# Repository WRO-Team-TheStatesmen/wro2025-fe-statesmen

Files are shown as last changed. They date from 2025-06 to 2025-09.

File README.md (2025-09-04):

<center><h1> The Statesmen 2025 </center>

This repository contains all of the documentation for team The Statesmen in the World Robot Olympiad 2025, Future Engineers category. This README.md file is the engineering notebook.

## Table of Contents
* [Our Team](#our-team)
  * [Atharv Baluja](#atharv-baluja)
  * [Arham Jain](#arham-jain)
  * [Yashvardhan Surana](#yashvardhan-surana)
* [Robot Photos](#robot-photos)
* [Performance Videos](#robot-videos)
* [Mobility Management](#mobility-management)
  * [Motor](#motor)
  * [Motor Driver](#motor-driver)
  * [Rear Wheel Drive](#rear-wheel-drive)
  * [Servo Motor](#servo-motor)
  * [Ackermann Steering System](#ackermann-steering-system)
  * [Robot Chassis](#chassis)
  * [Code Snippets](#code-snippets)
  * [Problems Faced and Solutions](#problems-we-faced-and-how-we-solved-them)
  * [Possible Improvements](#possible-improvements)
* [Power and Sense Management](#power-and-sense-management)
  * [Li-Ion Battery](#li-ion-battery)
  * [Buck Convertor](#lm2596-buck-converter)
  * [LiPo Battery](#lipo-battery)
  * [ESP32](#esp32-devkit-sbm)
  * [Raspberry Pi 5](#raspberry-pi-5-sbc)
  * [Camera](#camera)
  * [TF Luna LiDAR Sensor](#tf-luna-lidar-sensor)
  * [BNO055 Orientation Sensor](#bno055-orentiation-sensor)
  * [Power System Connections](#connection-diagram-for-power-system)
  * [Sensor Connections](#connection-diagram-for-sensors)
  * [Code Snippets](#code-snippets-for-components)
  * [Problems Faced and Solutions](#problems-we-faced-and-how-we-solved-them-1)
  * [Possible Improvements](#potential-improvements)
* [Obstacle Management](#obstacle-management)
  * [Open Challenge](#open-challenge)
  * [Obstacle Challenge](#obstacle-challenge)
  * [Problems Faced](#problems-we-faced-and-how-we-solved-them-2)
  * [Possible Improvements](#potential-improvements-1)
* [Engineering Factor](#engineering-factor)
* [Software Integration](#software-integration)
  * [System Architecture](#system-architecture)
  * [Communication Protocol](#communication-protocol)
  * [Code Modularity](#code-modularity)
  * [Communication API](#communication-api)
  * [Debugging](#debugging)
* [Robot Construction Guide](#robot-construction-guide)

## Our Team

### Team Photo
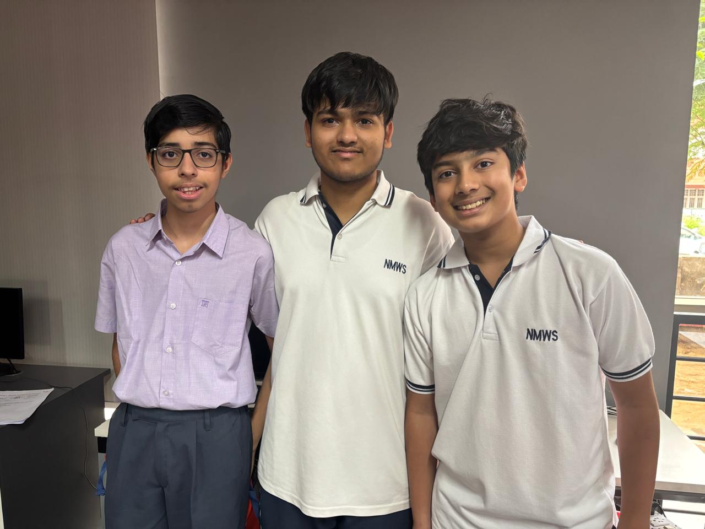
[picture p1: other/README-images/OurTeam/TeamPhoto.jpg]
Team Photo


### Atharv Baluja
<strong>Age: </strong>14

<strong> School: </strong> Neerja Modi World School

<strong>Description: </strong>
Hey! I am Atharv. I'm a high school freshman from Jaipur, India. This is my second WRO seaon. Last year, I had participated in the Future Innovator category. This year, I wanted a bigger challenge so I am participating in the Future Engineers category. I am working on the software of the robot.

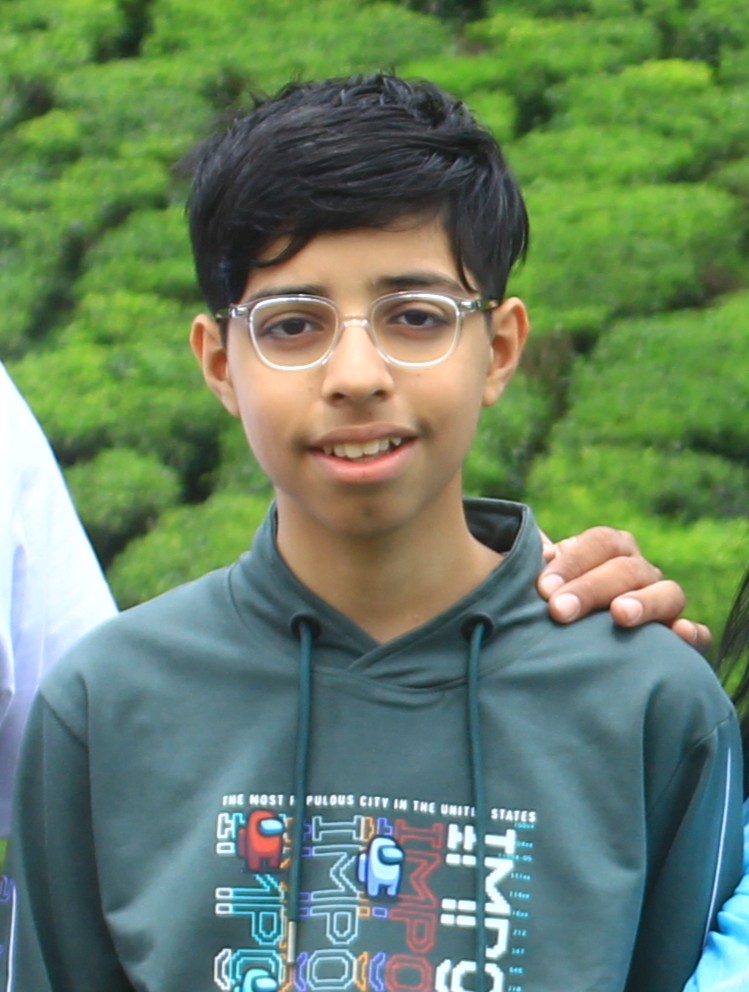
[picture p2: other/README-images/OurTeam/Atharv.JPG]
Atharv Baluja


### Arham Jain
Hello, I am Arham, an 11th-grade student at Neerja Modi School. I have competed in WRO once before in the Future Innovators category two years ago. I was preparing to compete in the Future Engineers category last year before some hurdles derailed my progress. Building on the knowledge and research from last year, I hope to put my effort into the Future Engineers Category again.

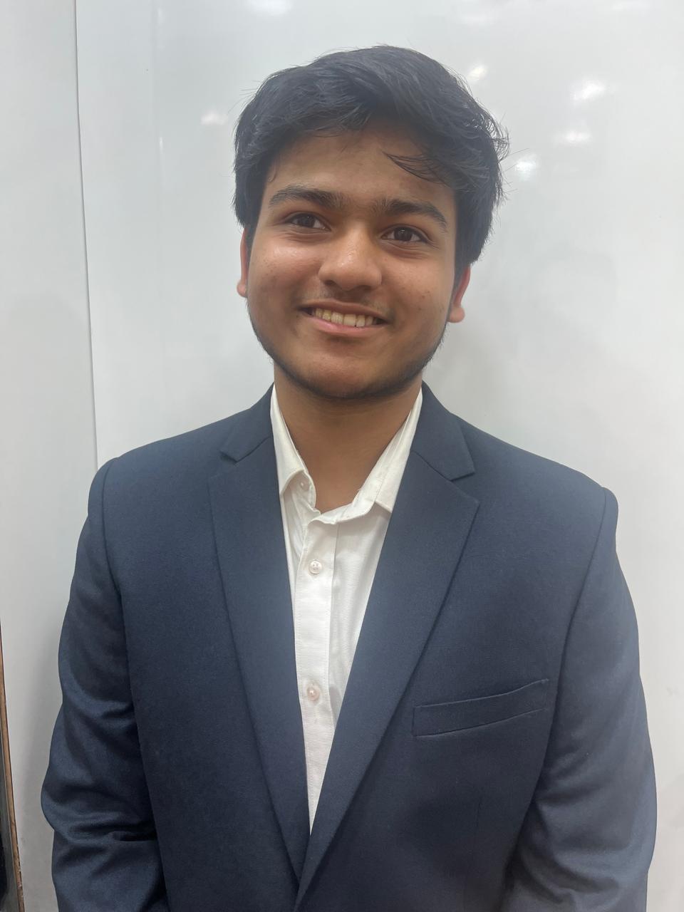
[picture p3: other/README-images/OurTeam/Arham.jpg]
Arham Jain


### Yashvardhan Surana
Hello, I'm Yash. I am a 6th grader from Jaipur. This is my second time participating in WRO. Last year, I had participated in the Future Innovators category. This year, I'm taking part in the Future Engineers category in the team The Statesmen. In The Statesmen, I am in charge of the hardware of the robot.

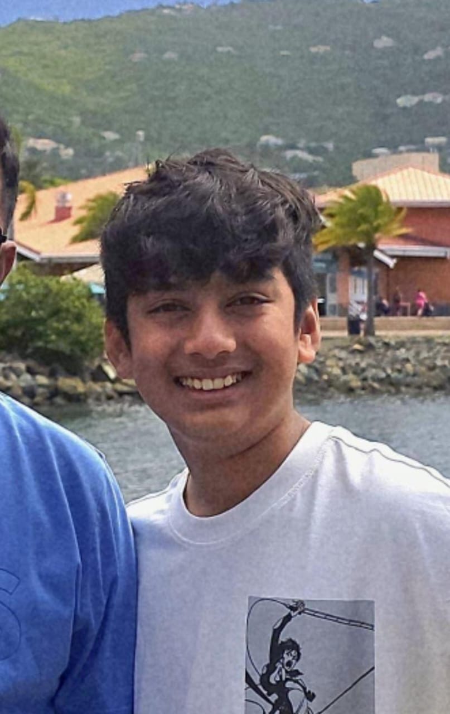
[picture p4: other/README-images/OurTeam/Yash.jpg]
Yashvardhan Surana


## Robot Photos
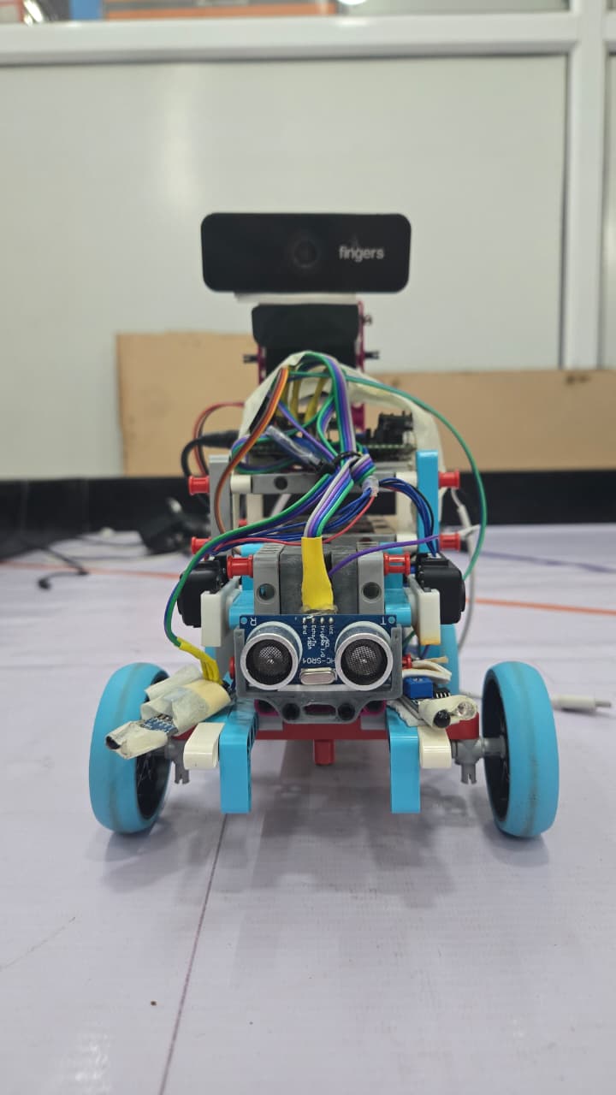
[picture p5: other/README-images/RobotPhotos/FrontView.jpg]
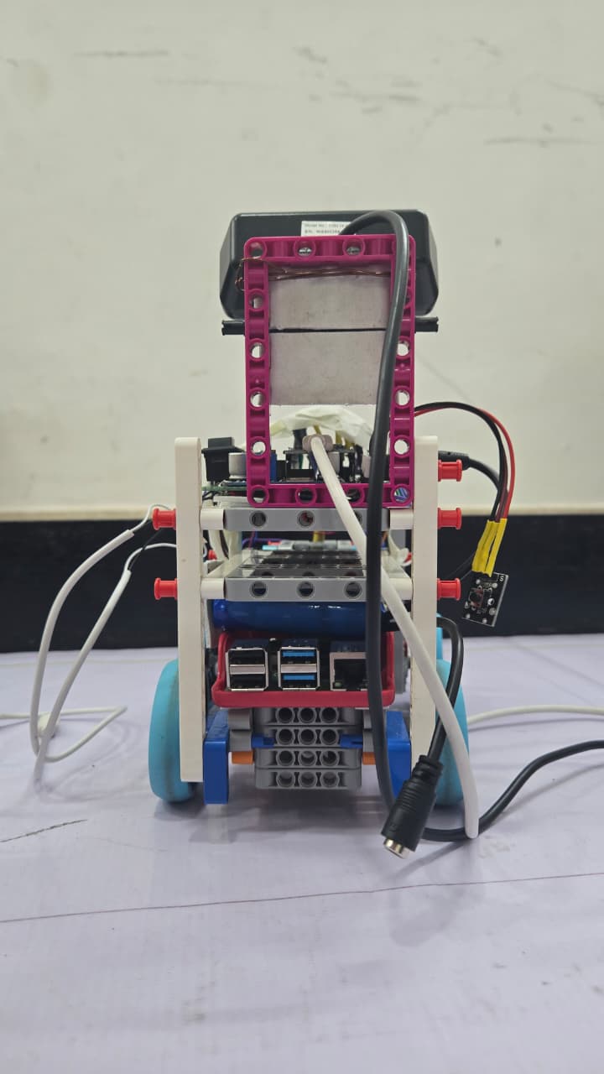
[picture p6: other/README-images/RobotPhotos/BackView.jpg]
|  |  | 
| :--: | :--: |
| *Front View* | *Back View* |
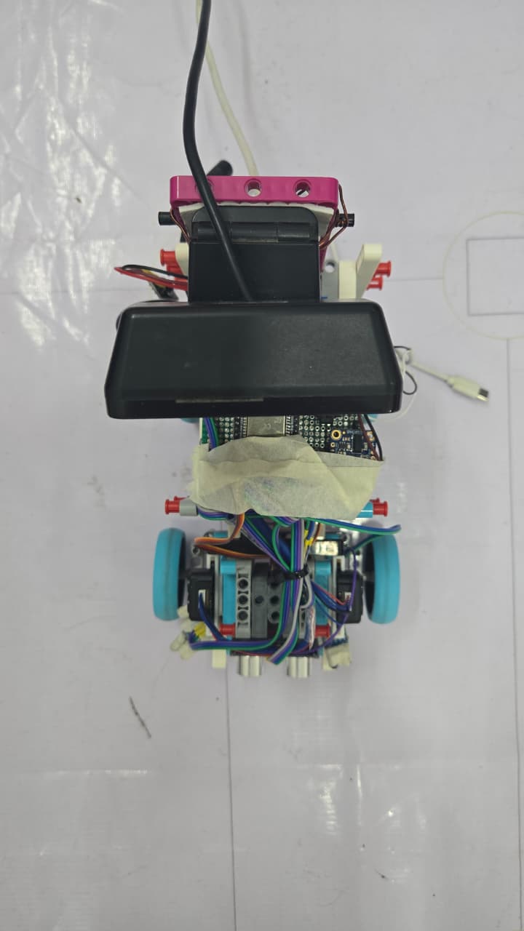
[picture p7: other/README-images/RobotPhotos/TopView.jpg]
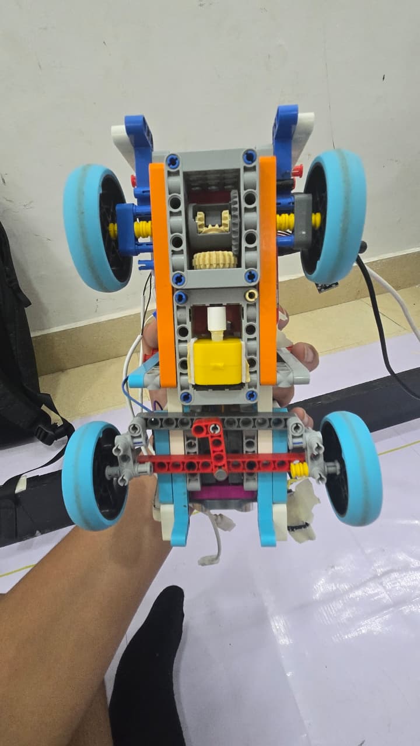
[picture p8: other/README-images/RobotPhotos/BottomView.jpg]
|  |  | 
| *Top View* | *Bottom View* |
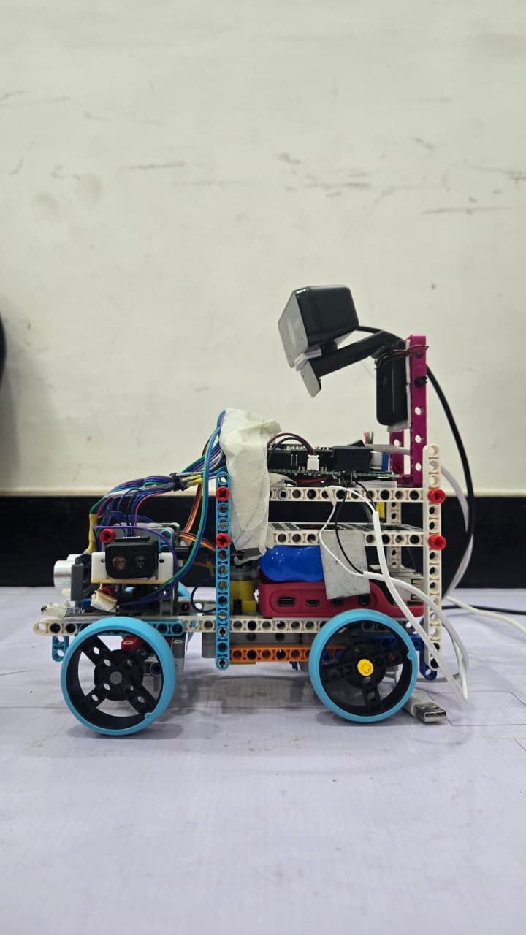
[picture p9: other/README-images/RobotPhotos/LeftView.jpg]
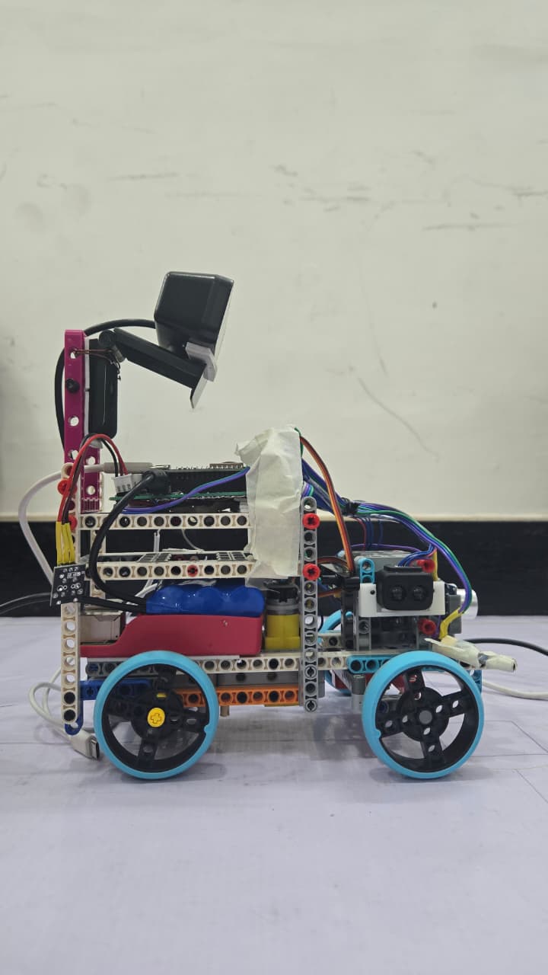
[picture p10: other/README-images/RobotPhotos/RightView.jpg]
|  |  | 
| *Left View* | *Right View* |

## Robot Videos
### Open Challenge - Default Setup
<video width="640" height="360" controls>
  <source src="./other/README-images/RunVideos/OpenChallenge1.mp4" type="video/mp4">
  Your browser does not support the video tag.
</video>

If the video is not loading for you, you can view it [here](https://youtu.be/yJYID6W3fv8)

### Open Challenge - 1 Side Extended
<video width="640" height="360" controls>
  <source src="./other/README-images/RunVideos/OpenChallenge2.mp4" type="video/mp4">
  Your browser does not support the video tag.
</video>

If the video is not loading for you, you can view it [here](https://youtu.be/VSAF0O4e32w)

### Open Challenge - 2 Sides Extended
<video width="640" height="360" controls>
  <source src="./other/README-images/RunVideos/OpenChallenge3.mp4" type="video/mp4">
  Your browser does not support the video tag.
</video>

If the video is not loading for you, you can view it [here](https://youtu.be/7XdKwXTz3Lk)

### Obstacle Challenge - Setup 1
You can view this video [here](https://www.youtube.com/watch?v=GN4vLTXXRtY)

You can watch all the videos on our [youtube channel](https://www.youtube.com/@TheStatesmen-fe)

## Mobility Management
Our robot's mobility is managed by multiple components - a BO DC motor, L293D motor driver, an MG90 servo motor connected to a Ackermann steering geometry, and a rear differential. All of these seamlessly work together to achieve efficient movement.

### Motor
Aftering considering multiple motors, we finally settleed on a DC BO motor. We considered factors like speed (RPM), torque (kg cm), weight (g), required voltage (v), and current consumption (mA).

<table>
  <tr>
    <td width="50%" style="text-align: left;">
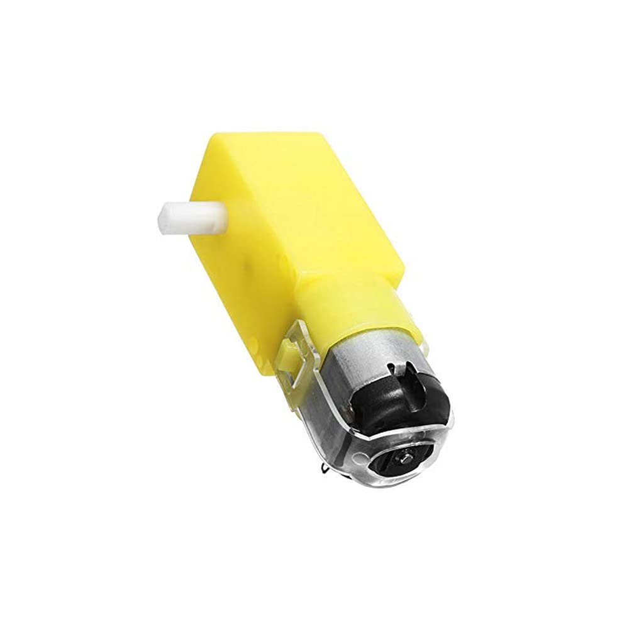
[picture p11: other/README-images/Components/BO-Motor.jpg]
DC BO Motor
      
    </td>
    <td width="50%" style="text-align: left; vertical-align: top;">
      <h3>Specifications:</h3>
      <li>Voltage: 12V</li>
      <li>Gear Ratio: 1:50</li>
      <li>Speed: 400 ± 20% rpm</li>
      <li>Rated Torque: 0.35 kg·cm</li>
      <li>Weight: 28g</li>
      <li>No Load Current Consumption: 40-180 mA</li>
      </li>
    </td>
  </tr>
</table>

You can buy this motor [here](https://robu.in/product/300-rpm-bo-motor-straight)

To connect this motor to a Lego-compatible axle, we 3D-printed a custom adapter

<table>
  <tr>
    <td width="50%" style="text-align: left;">
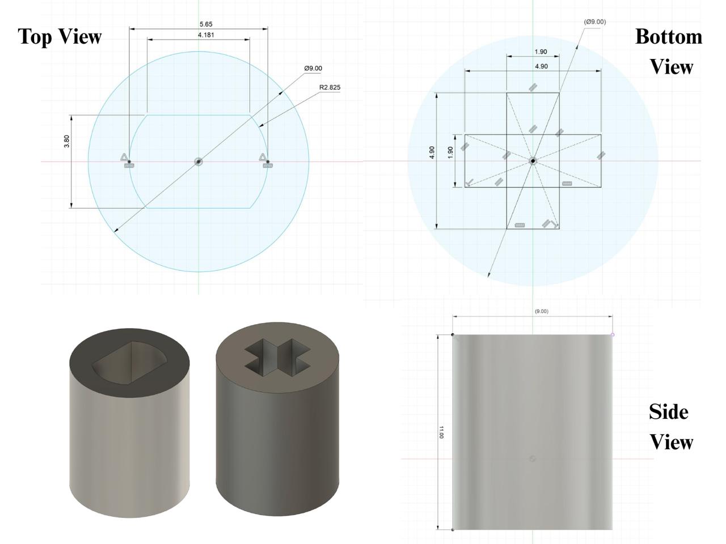
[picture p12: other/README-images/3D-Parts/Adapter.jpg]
Motor-Axle Adapter
      
    </td>
  </tr>
</table>

This is a female-to-female adapter

### Motor Driver
At first, we used the L298N Dual H-Bridge motor driver. The problem with that was that it was big because of the heatsink and the module wasn't built efficiently. After evaluating more options, we settled on the L293D motor driver. This is just like the L298N but is a small IC instead of a big module.

<table>
  <tr>
    <td width="50%" style="text-align: left;">
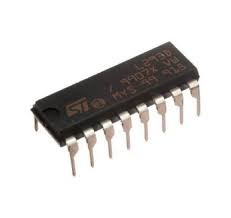
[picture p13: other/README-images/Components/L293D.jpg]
L293D Motor Driver IC
      
    </td>
    <td width="50%" style="text-align: left; vertical-align: top;">
      <h3>Specifications:</h3>
      <li>Type: Dual H-Bridge</li>
      <li>Power Supply Voltage: 4.5v to 36v</li>
      <li>Logic Voltage: 4.5v to 7v</li>
      <li>2 DC Motors</li>
      <li>Internal ESD Protection</li>
      </li>
    </td>
  </tr>
</table>

We are using the following pin connections for the motor driver:
<ol>
<li>Enable 1,2 - For PWM speed control of motor A</li>
<li>Input 1 - Direction control pin 1 for motor A</li>
<li>Output 1 - Connected to one terminal of motor A</li>
<li>GND - Ground</li>
<li>GND - Ground</li>
<li>Output 2 - Connected to other terminal of motor A</li>
<li>Input 2 - Direction control pin 2 for motor A</li>
<li>VCC 2 - Power supply (+)</li>
<li>Enable 3,4 - For PWM speed control of motor B</li>
<li>Input 3 - Direction control pin 1 for motor B</li>
<li>Output 3 - Connected to one terminal of motor B</li>
<li>GND - Ground</li>
<li>GND - Ground</li>
<li>Output 4 - Connected to other terminal of motor B</li>
<li>Input 4 - Direction control pin 2 for motor B</li>
<li>VCC 1 - Power Supply (+) for logic</li>
</ol>

### Rear Wheel Drive
We have achieved RWD with the motor connected to a lego rear differential. We have used the lego parts to minimize friction.

<table>
    <td width="50%" style="text-align: left;">
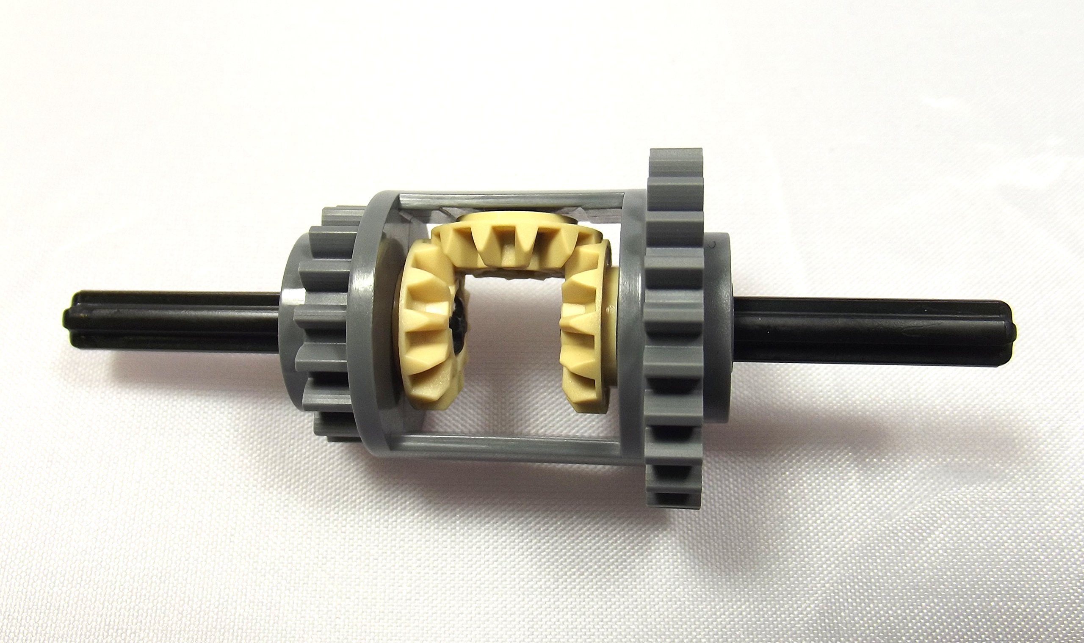
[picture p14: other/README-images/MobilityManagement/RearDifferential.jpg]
Lego Rear Differential
      
    </td>
    <td width="50%" style="text-align: left;">
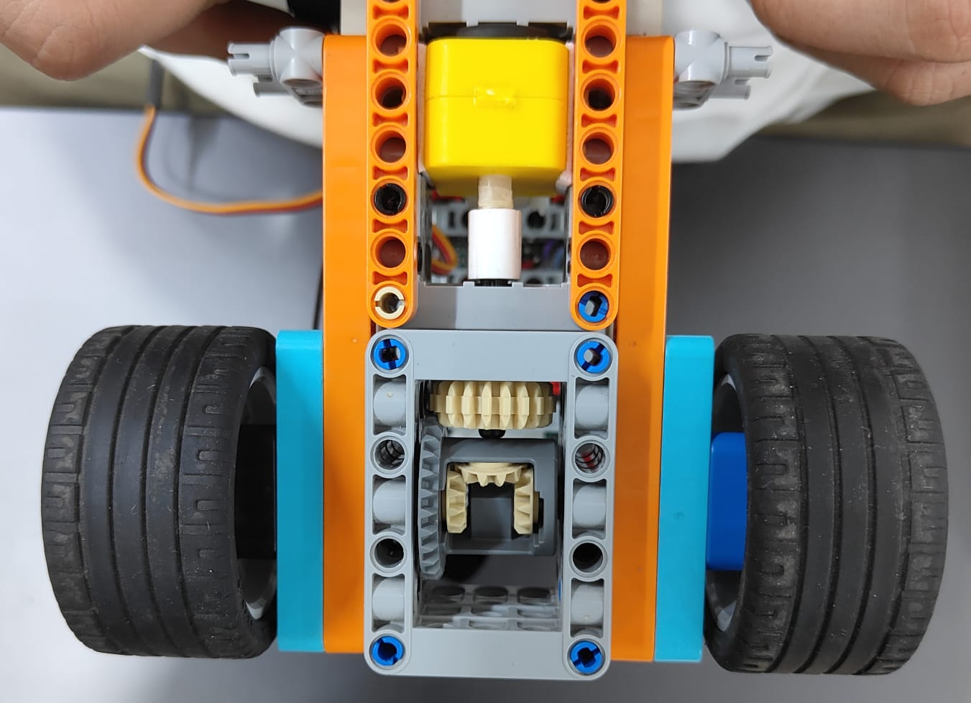
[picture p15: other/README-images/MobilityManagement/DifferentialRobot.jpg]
Lego Rear Differential
      
    </td>
</table>

Rear Differential GIF

### Servo Motor
We are using an ackermann steering geometry to steer the robot. This system runs with an MG90 servo motor.

<table>
  <tr>
    <td width="50%" style="text-align: left;">
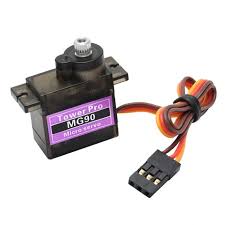
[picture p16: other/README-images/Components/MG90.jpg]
MG90 Servo Motor
      
    </td>
    <td width="50%" style="text-align: left; vertical-align: top;">
      <h3>Specifications:</h3>
      <li>Angle Constaint: 0° to 360°</li>
      <li>Input Voltage: 4.8v to 6v</li>
      <li>Stall Torque: 1.8 kg/cm</li>
    </td>
  </tr>
</table>

Here is the pinout of the MG90 Servo Motor:
<ol>
<li>VCC - Red Wire - 5V</li>
<li>Signal - Orange Wire - PWM</li>
<li>Ground - Black Wire - GND</li>
</ol>

To connect the servo motor to the steering geometry, we created a 3D-printed adapter which converted the servo rotor into a lego compatible axle.

<table>
  <tr>
    <td width="50%" style="text-align: left;">
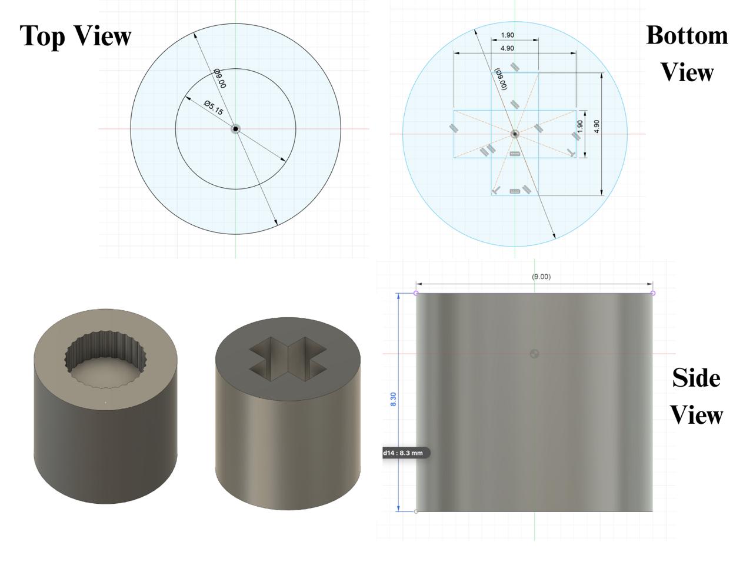
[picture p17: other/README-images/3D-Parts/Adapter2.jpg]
Servo Adapter
      
    </td>
  </tr>
</table>

It is a female-to-female adapter.

### Ackermann Steering System

We are using the Ackermann steering system. This system allows the front 2 wheels to turn at different angles, allowing for sharper turns and decreasing friction due to drag.

<table>
  <tr>
    <td width="50%" style="text-align: left;">
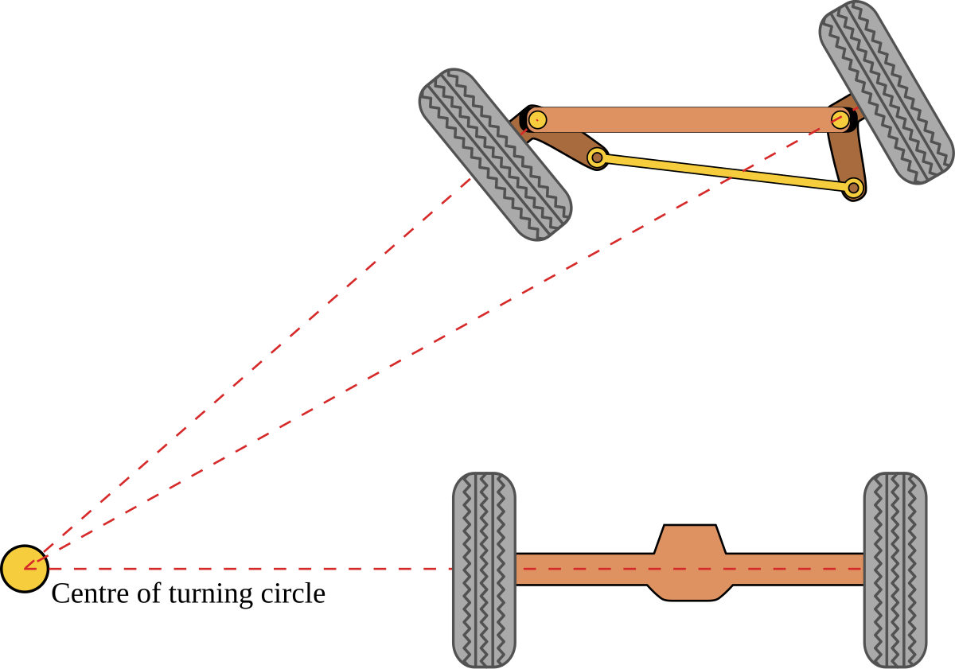
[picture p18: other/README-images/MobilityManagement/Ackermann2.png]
Ackermann Steering
      
    </td>
  </tr>
  <tr>
    <td width="50%" style="text-align: left;">
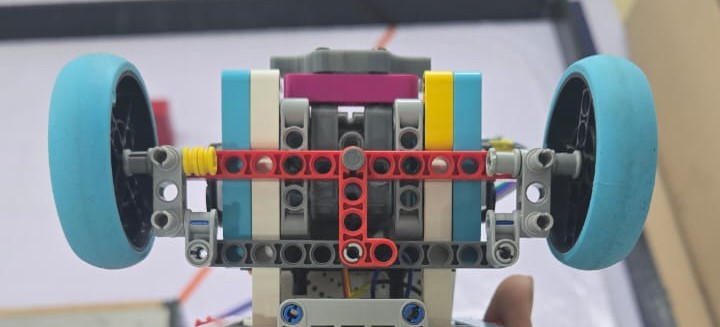
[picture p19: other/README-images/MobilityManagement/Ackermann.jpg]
Ackermann Steering
      
    </td>
  </tr>
</table>

Steering System GIF

### Chassis
#### Photos
|  |  | 
| :--: | :--: |
| *Orthographic View 1* | *Orthographic View 2* |
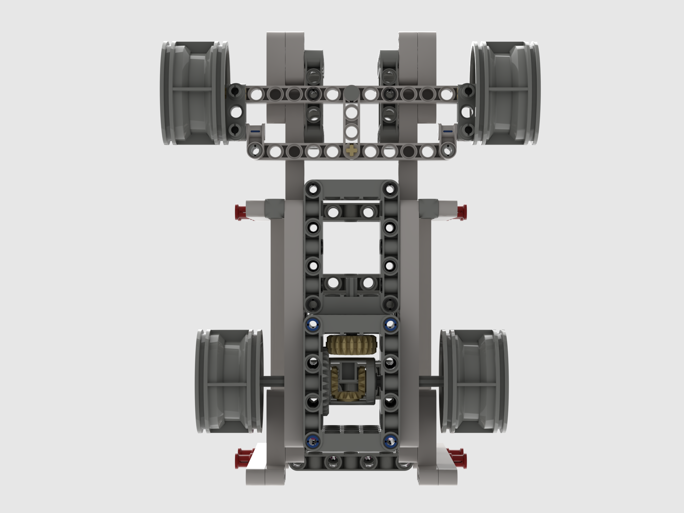
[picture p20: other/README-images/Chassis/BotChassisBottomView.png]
|  |  | 
| *Top View* | *Bottom View* |
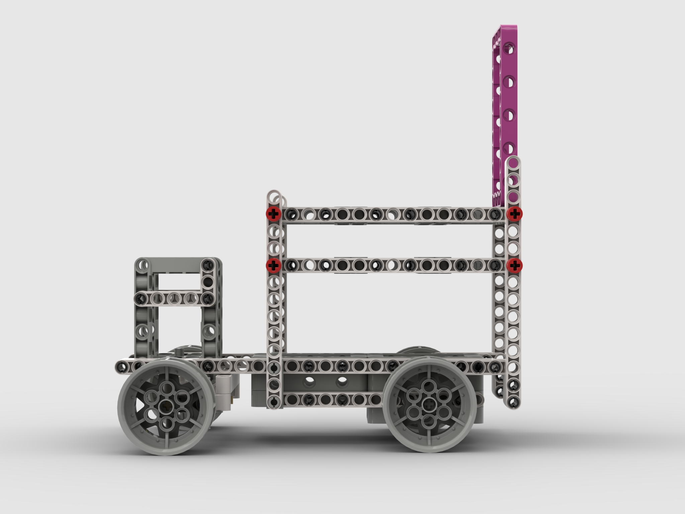
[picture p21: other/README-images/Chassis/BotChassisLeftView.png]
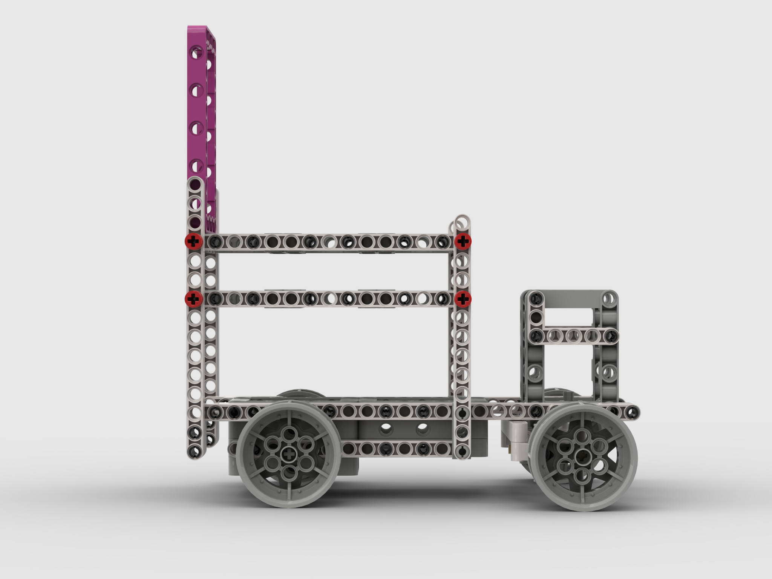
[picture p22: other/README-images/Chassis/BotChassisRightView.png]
|  |  | 
| *Left View* | *Right View* |

Robot Chassis GIF

#### Assembly Guide

<embed src="./other/README-images/Chassis/ChassisAssembly.pdf" type="application/pdf" width="100%" alt="Chassis Assembly Guide PDF"> </embed>

If the PDF is not loading properly, you can view the guide [here](https://github.com/WRO-Team-TheStatesmen/wro2025-fe-statesmen/blob/main/other/README-images/Chassis/ChassisAssembly.pdf)

### Connection Diagram for Mobility System
<table>
  <tr>
    <td width="50%" style="text-align: left;">
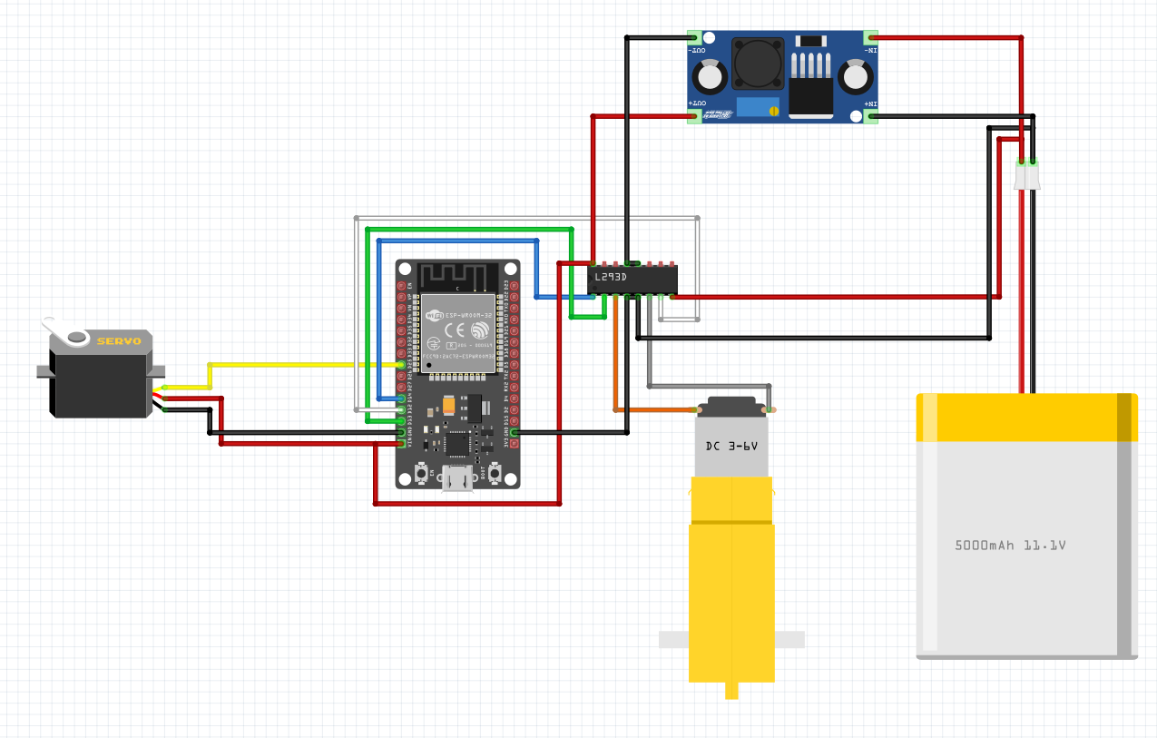
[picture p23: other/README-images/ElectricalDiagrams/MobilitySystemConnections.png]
Mobility System Connections
      
    </td>
  </tr>
</table>

### Code Snippets
#### Running the L293D Motor Driver with an ESP32 Devkit
```
// Program for running the motors via the L293D motor driver IC on an ESP32 devkit

#define IN1 13
#define IN2 12
#define ENA 14

void setup() {
  pinMode(IN1, OUTPUT);
  pinMode(IN2, OUTPUT);
  pinMode(ENA, OUTPUT);
}

void loop() {
  // Forward
  digitalWrite(IN1, HIGH);
  digitalWrite(IN2, LOW);
  analogWrite(ENA, 255);
  delay(2000);

  // Stop
  analogWrite(ENA, 0);
  delay(1000);

  // Backwards
  digitalWrite(IN1, LOW);
  digitalWrite(IN2, HIGH);
  analogWrite(ENA, 255);
  delay(2000);

  // Stop
  analogWrite(ENA, 0);
}
```

#### Running the MG90 Servo Motor with an ESP32 Devkit
```
// Program for rotating the steering MG90 servo motor connected to an ESP32 devkit [signal pin = 25]

const int servoPin = 25;
const int servoCenter = 138; // Servo center is the position of the servo at which the steering system is centered

void moveServoAngle(int angle){
  angle = constrain(angle,0,180);
  int pulsewidth = map(angle,0,180,500,2400);
  digitalWrite(servoPin, HIGH);
  delayMicroseconds(pulsewidth);
  digitalWrite(servoPin, LOW);
  delay(20 - pulsewidth/1000);
}

void steer(int angle) {
  moveServoAngle(servoCenter + angle);
}

void setup() {
  pinMode(servoPin, OUTPUT);
}

void loop() {
  steer(0);
  delay(1000);
  steer(30);
  delay(1000);
  steer(0);
  delay(1000);
  steer(-30);
  delay(1000);
}
```

### Problems We Faced and How We Solved Them
<ol>
<li> <strong>Bot Rear Skidding: </strong> At first, we were not using a rear differential but rather the motor connected to a gear which rotated a single axle which both the wheels were on. There was a huge problem with this. As shown in the image below, both wheeels have to move a different distance.<br><br>

<table>
  <tr>
    <td width="50%" style="text-align: left;">
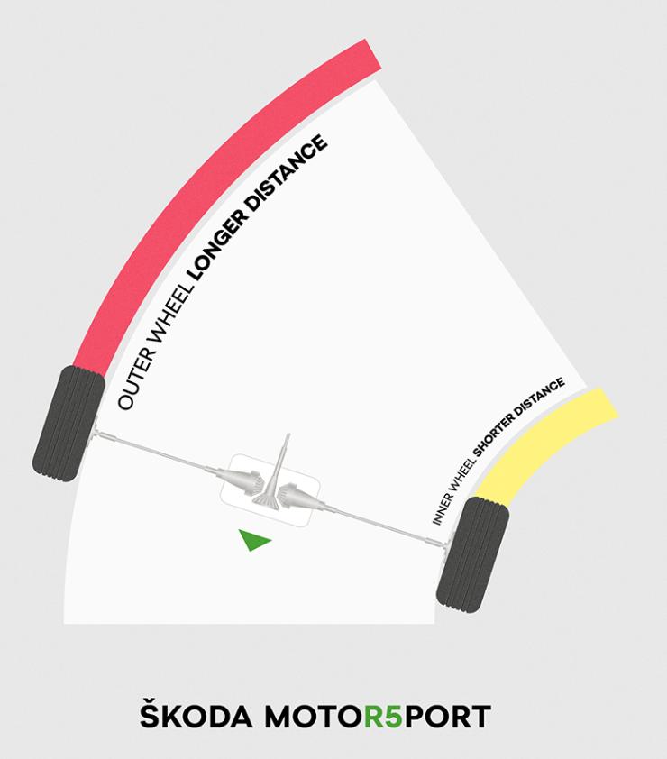
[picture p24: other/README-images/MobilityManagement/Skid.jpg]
Wheel Distance Difference
      
    </td>
  </tr>
</table>

To fix this, we added the <strong>Rear Differential</strong>. This allows the 2 wheels to move at different speeds while only using one motor.
</li>
<li> <strong>Bot Front Skidding: </strong> At first, we were using a parallel steering geometry. The same problem occurred. There was a lot of friction and drag. This limited the maximum turning angle of the robot.
<br><br>

Steering System GIF

As you can see, in this system, both the wheels are turned equally. This does not achieve peak efficiency. That is why we switched to the ackermann system.
</li>

<li>
<strong>Axle Sliiping Out of Differential</strong>

Initially, the axle used in the differential was too small. Because of vibrations, it often slipped out of the differential, which caused the gears to come out and completely ruined the robot's movement. If we used longer axles, it would stick out of the robot and could touch other blocks.

To fix this, we did two things. Firstly, we structured the chassis of the robot since there were some redundant pieces. We also switched out the rear tyres to the normal blue tyres since it would fix the problem without causing a significant change in the movement of the robot.
</li>

<li>
<strong>No Exact Piece for Ackermann</strong>: While trying to create the ackermann steering geometry, we noticed that no single piece could create the steering geometry. At first, we used this piece:

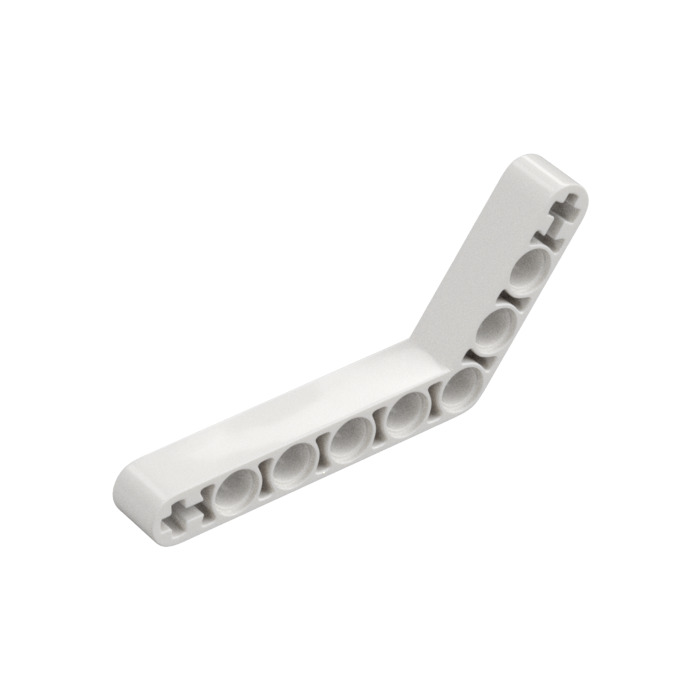
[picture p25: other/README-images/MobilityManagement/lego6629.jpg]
Lego Piece 6629


However, using this caused a problem that the robot wasn't fully level. After trying out multiple options, we finally settled on joining 2 pieces to achieve this:

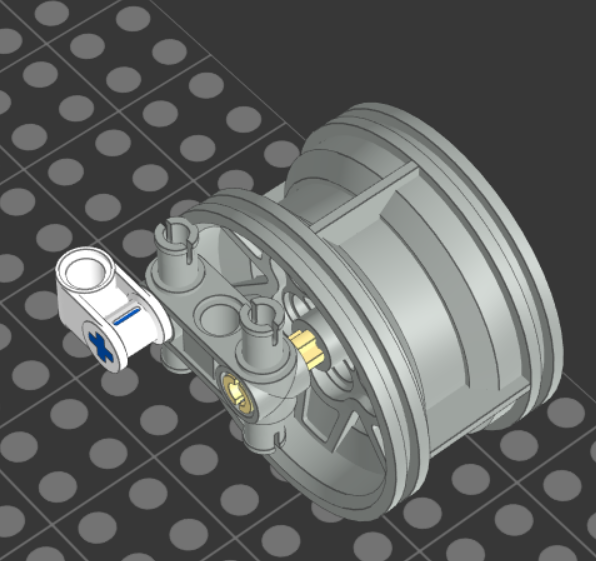
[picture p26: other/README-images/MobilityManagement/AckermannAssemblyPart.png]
Ackermann Assembly Part


With this, we encountered another problem. If we tried to turn it more than 40 degree, it would cause a lot of tension and the 2 pieces would disconnect. To increase the maximum turning angle to 60 degrees, we had to superglue the 2 pieces together.
</li>
</ol>

### Possible Improvements
<ol>
<li><strong>Using a Higher RPM Motor</strong> so that the robot can move faster</li>
<li><strong>Using a Motor with an Encoder</strong> so that the robot movements become more accurate and precise</li>
<li><strong>Using Metal Gears for the Rear Differential</strong> so that it can withstand higher speeds</li>
<li><strong>Using a Heat Sink or Active Cooling for the Motor Driver</strong> so that it doesn't get too hot much while being used</li>
<li><strong>Using Four-Wheel Drive</strong> for better movement</li>
<li><strong>Using All-Wheel Steering</strong> for better and faster turning</li>
<li><strong>Using a Custom Gearbox</strong> instead of relying on the BO motor's gear ratio to create an optimized gear ratio</li>
<li><strong>Using a Fully 3D Printed Chassis</strong> instead of using lego parts so that the robot is as light as possible</li>
</ol>

## Power and Sense Management
Our robot uses an 11.1v Li-ion Battery and a 2500 mAh 3C 11.1v LiPo battery for power with a buck converter. An ESP32 Devkit single board microcontroller is used with a Raspberry Pi 5 single board computer. Along with this, 4 TF Luna LiDAR sensors (one at the left, two at the front, and one at the back) are used for disance measurement and a BNO055 orientation sensor to measure the rotation.

### Li-Ion Battery
We are using an 11.1v Li-ion battery pack
<table>
  <tr>
    <td width="50%" style="text-align: left;">
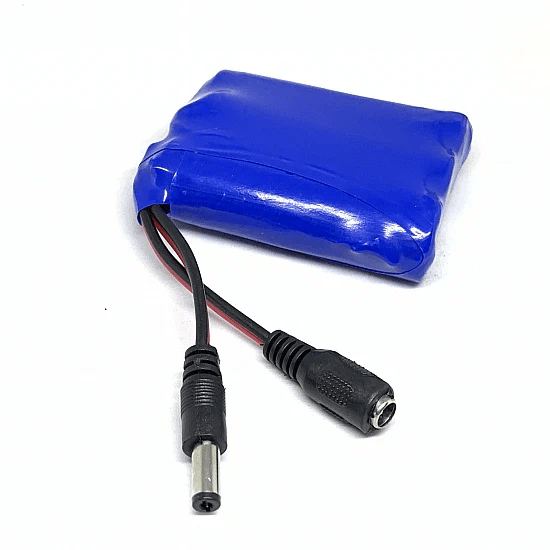
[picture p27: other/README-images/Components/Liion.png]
11.1V Li-ion Battery
      
    </td>
    <td width="50%" style="text-align: left; vertical-align: top;">
      <h3>Specifications:</h3>
      <li>Voltage: 11.1V</li>
      <li>Capacity: 2200mAh</li>
      <li>Discharge Rate: 2C</li>
      <li>Maximum Current: Capcity x Discharge Rate = 4.8A</li>
    </td>
  </tr>
</table>

This battery pack consists of 3 18650 3.7v Li-ion cells

This battery powers the motors, ESP32, and all the sensors

You can buy this battery [here](https://www.amazon.in/2200MAH-Rechargeable-Battery-Robotics-Vehicle/dp/B0DNZJ7823/)

### LM2596 Buck Converter
We are using an 11.1v battery, but the ESP32 requires 5v to be provided to it. To convert the 11.1v to 5v, we are using an LM2596 DC-DC Buck Converter

<table>
  <tr>
    <td width="250x" style="text-align: left;">
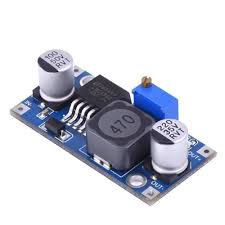
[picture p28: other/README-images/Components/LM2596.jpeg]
LM2596 Buck Converter
      
    </td>
    <td width="500px" style="text-align: left; vertical-align: top;">
      <h3>Specifications:</h3>
      <li>Supply Voltage: 3v - 40v</li>
      <li>Output Voltage: 1.5v - 35v (adjustable) --> Set to 5v for us</li>
      <li>Output Current: Rated 2A, Maximum 3A</li>
      <li>Switching Frequency: 150KHz</li>
      <li>Conversion Efficiency: 92%</li>
    </td>
  </tr>
</table>

You can buy the LM2596 Buck Converter [here](https://robu.in/product/lm2596s-dc-dc-buck-converter-power-supply/)

### LiPo Battery
We are using a lithium polymer (LiPo) battery to power the Raspberry Pi.
<table>
  <tr>
    <td width="250x" style="text-align: left;">
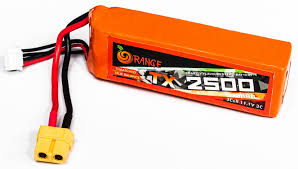
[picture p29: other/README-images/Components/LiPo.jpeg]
LiPo battery
      
    </td>
    <td width="500px" style="text-align: left; vertical-align: top;">
      <h3>Specifications:</h3>
      <li>Output Voltage: 11.1v</li>
      <li>Capacity: 2500 mAh</li>
      <li>Discharge Rate: 3C</li>
      <li>Maximum Current: 3C * 2.5Ah = 7.5A</li>
    </td>
  </tr>
</table>

### ESP32 Devkit SBM
We are using an ESP32 Devkit single board microcontroller.

<table>
  <tr>
    <td width="250x" style="text-align: left;">
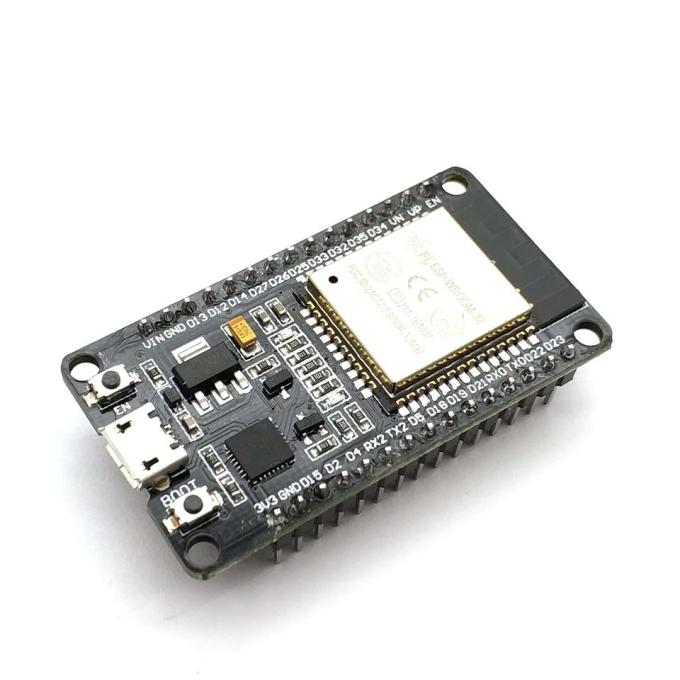
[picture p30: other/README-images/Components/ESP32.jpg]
ESP32 Devkit
      
    </td>
    <td width="500px" style="text-align: left; vertical-align: top;">
      <h3>Specifications:</h3>
      <li>Supply Voltage: 5v</li>
      <li>Power Consumption: 150mA - 250mA</li>
      <li>GPIO Pins: 25</li>
      <li>Clock Speed: 240MHz</li>
      <li>Flash Memory: 4 MB</li>
      <li>SRAM: 520 KB</li>
    </td>
  </tr>
</table>

We chose this microcontroller over others because of its high clock speed and processing power.

Here is the pinout diagram for this ESP32:

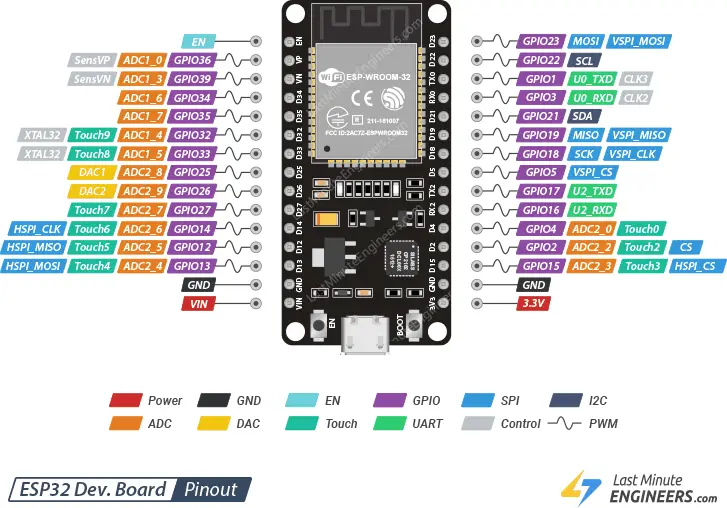
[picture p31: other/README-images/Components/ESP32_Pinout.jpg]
ESP32 Devkit Pinout


### Raspberry Pi 5 SBC
We are using the Raspberry Pi 5 Model B 8 GB RAM single board computer. We have chosen this after considering multiple options. We ended up on this one because of its cost and technical specifications mentioned below.

<table>
  <tr>
    <td width="250x" style="text-align: left;">
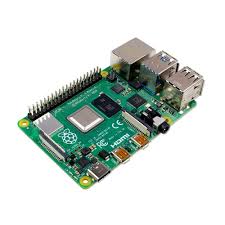
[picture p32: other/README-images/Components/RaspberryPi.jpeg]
Raspberry Pi 5
      
    </td>
    <td width="500px" style="text-align: left; vertical-align: top;">
      <h3>Specifications:</h3>
      <li>Supply Voltage and Current (Optimal): 5.1v at 5A</li>
      <li>CPU: Broadcom BCM2712 Quadcore Cortex-A76 - 64-bit SoC @ 2.4GHz</li>
      <li>RAM: 8GB</li>
      <li>USB Type A Ports: 4</li>
      <li>GPIO Pins: 28</li>
    </td>
  </tr>
</table>

Here is the pinout of the Raspberry Pi 5

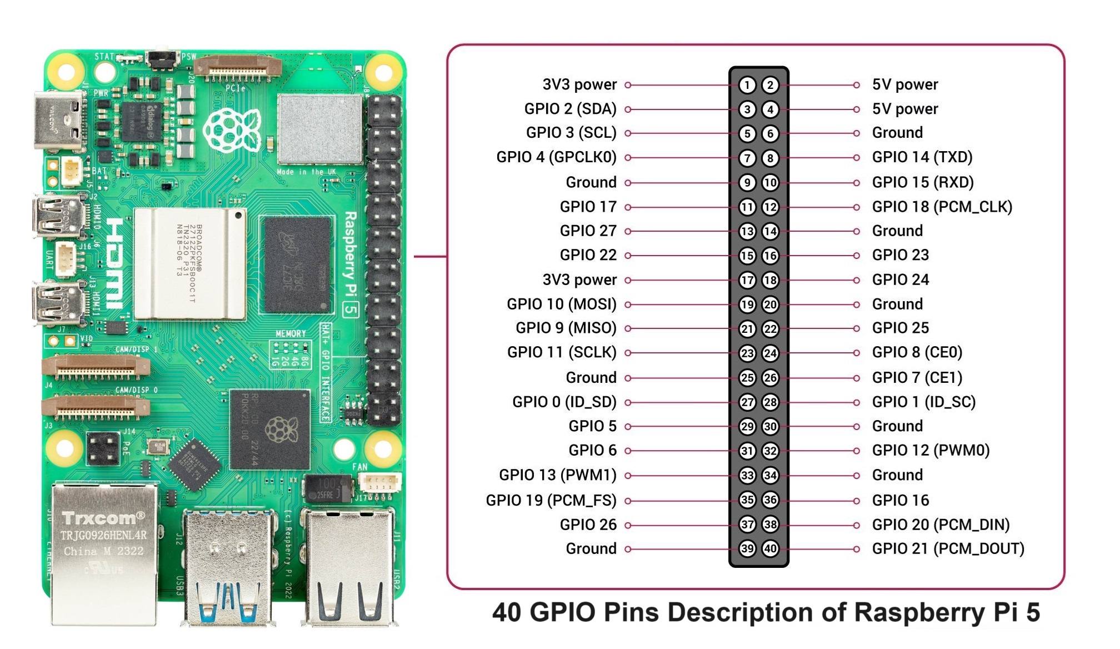
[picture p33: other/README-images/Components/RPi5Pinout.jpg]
Raspberry Pi 5 Pinout


### Camera
We are using the FINGERS 1080p Hi-Res camera. We chose this camera after considereing multiple factors like its field of view, high resolution, and color saturation.

<table>
  <tr>
    <td width="250x" style="text-align: left;">
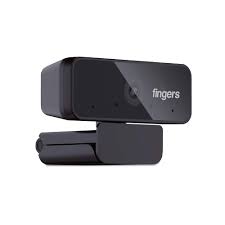
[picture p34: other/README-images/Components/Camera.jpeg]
Fingers 1080p Hi-Res Camera
      
    </td>
    <td width="500px" style="text-align: left; vertical-align: top;">
      <h3>Specifications:</h3>
      <li>Power Consumption: 200mA</li>
    </td>
  </tr>
</table>

### TF Luna LiDAR Sensor
We are using the TF-Luna LiDAR sensor to find the distances from the robot to the walls. We chose this sensor because of its speed, accuracy, and range.

<table>
  <tr>
    <td width="250x" style="text-align: left;">
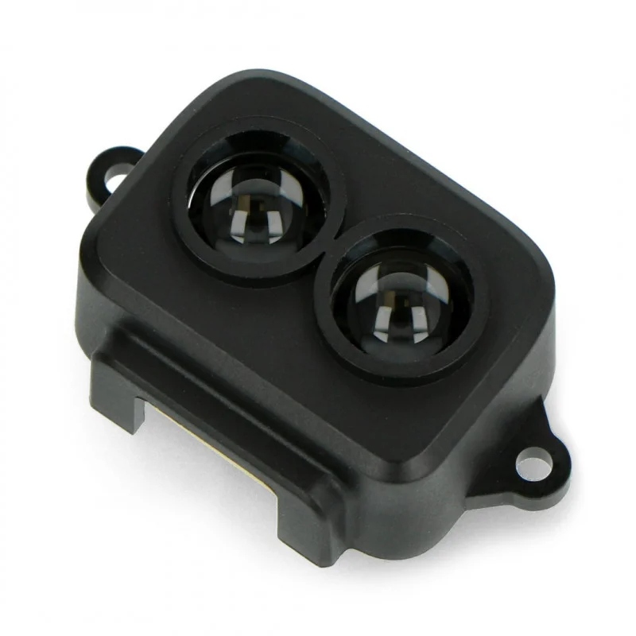
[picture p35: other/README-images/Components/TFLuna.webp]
TF Luna LiDAR Sensor
      
    </td>
    <td width="500px" style="text-align: left; vertical-align: top;">
      <h3>Specifications:</h3>
      <li>Supply Voltage: 5v</li>
      <li>Power Consumption: 70mA</li>
      <li>Range: 8m</li>
      <li>Resolution: 1cm</li>
      <li>Communication Protocol: I2C / UART</li>
      <li>Ranging Frequency: 1 to 250 Hz (100 Hz by default)</li>
  </tr>
</table>

Here is the pinout of the TF Luna LiDAR sensor:
<ul>
<li>Pin 1 - VCC (3.7v to 5.2v)</li>
<li>Pin 2 - RX (UART) or SDA (I2C)</li>
<li>Pin 3 - TX (UART) or SCL (I2C)</li>
<li>Pin 4 - GND</li>
<li>Pin 5 - CFG</li>
<li>Pin 6 - MUX</li>
</ul>

By default, it uses the UART communication protocol. However, if we connect the CFG pin to ground, it uses the I2C protocol. We are using the UART protocol. UART works by sending asynchronus data without the use of a clock signal. It uses a start and stop bit.

To connect this sensor to a Lego part, we 3D-printed a custom mount

<table>
  <tr>
    <td width="50%" style="text-align: left;">
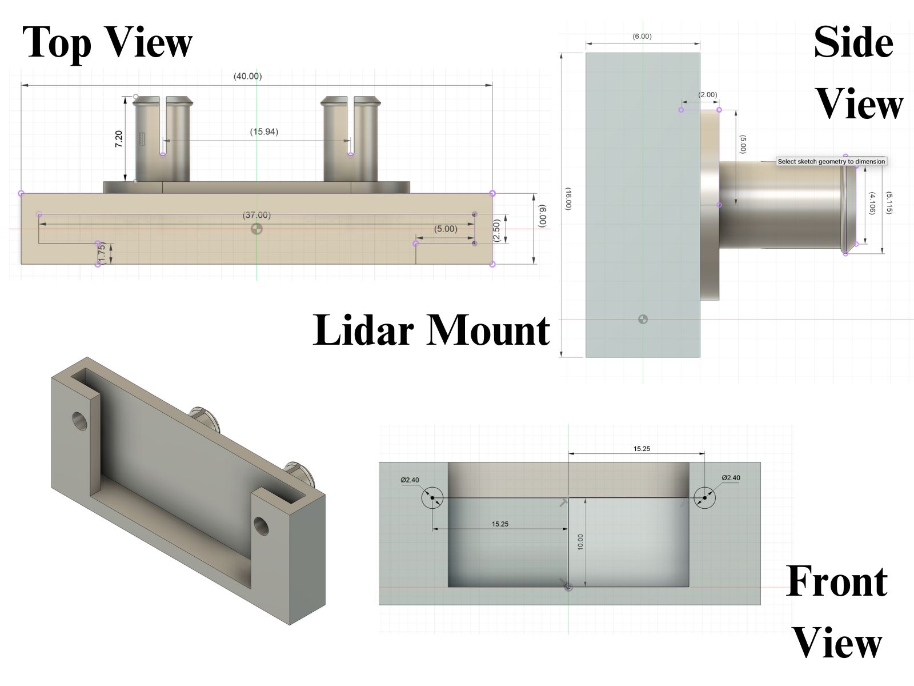
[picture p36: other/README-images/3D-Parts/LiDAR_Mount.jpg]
TF Luna LiDAR
      
    </td>
  </tr>
</table>

This is a female-to-female adapter

### BNO055 Orentiation Sensor
We are using the BNO055 Absolute Orientation Sensor. This sensor contains an accelerometer, a gyroscope, and a geomagnetic sensor. We chose this sensor after considering factors such as accuracy and weight.

<table>
  <tr>
    <td width="250x" style="text-align: left;">
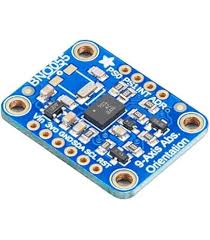
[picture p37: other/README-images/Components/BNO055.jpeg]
BNO055 Orientation Sensor
      
    </td>
    <td width="500px" style="text-align: left; vertical-align: top;">
      <h3>Specifications:</h3>
      <li>Supply Voltage: 3.3v or 5v</li>
      <li>Power Consumption: ~12.3mA</li>
      <li>Communication Protocol: I2C</li>
  </tr>
</table>

Here is the pinout of the BNO055 sensor:
<ul>
<li>Pin 1 - VCC (5v)</li>
<li>Pin 2 - VCC (3.3v)</li>
<li>Pin 3 - GND</li>
<li>Pin 4 - SDA</li>
<li>Pin 5 - SCL</li>
<li>Pin 6 - RST</li>
</ul>

### Connection Diagram for Power System
<table>
  <tr>
    <td width="50%" style="text-align: left;">
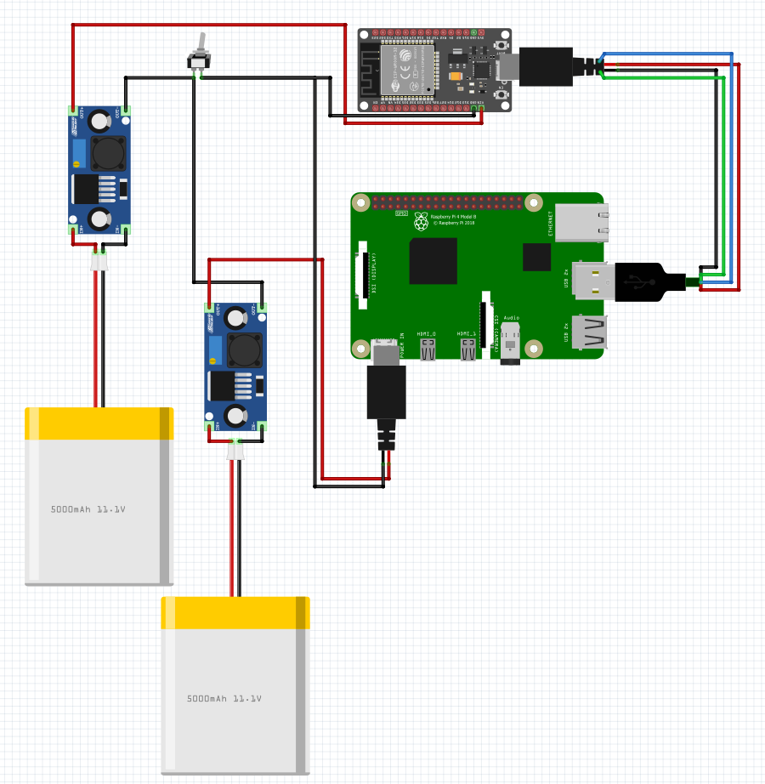
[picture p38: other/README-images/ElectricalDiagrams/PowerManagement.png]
Power System Connections
      
    </td>
  </tr>
</table>

### Connection Diagram for Sensors
#### Connection for Sensors Connected to ESP32
<table>
  <tr>
    <td width="50%" style="text-align: left;">
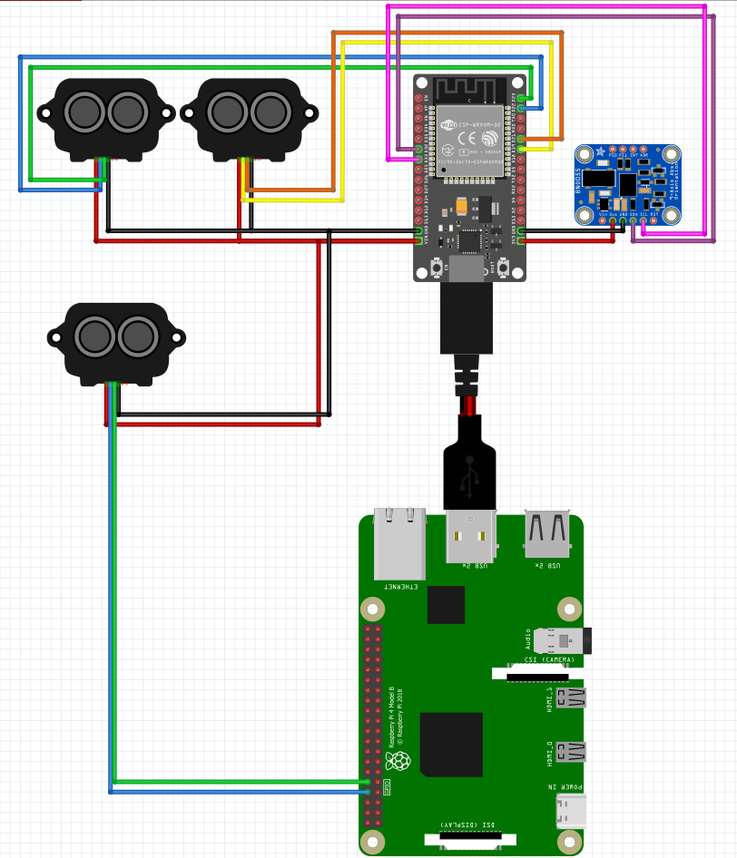
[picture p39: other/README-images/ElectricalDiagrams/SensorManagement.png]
      
    </td>
  </tr>
</table>

#### Connection for Sensors Connected to Raspberry Pi
<table>
  <tr>
    <td width="50%" style="text-align: left;">
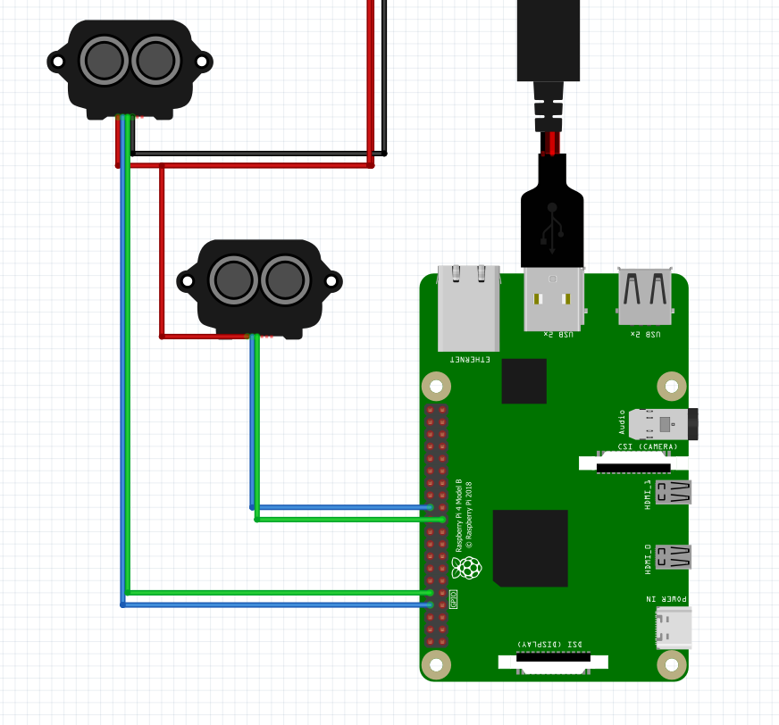
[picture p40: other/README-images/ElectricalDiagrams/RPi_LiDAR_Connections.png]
Sesnsor System Connections
      
    </td>
  </tr>
</table>

We connected the third TF Luna to the Raspberry Pi. This is because of two reasons:
1. The ESP32 only supports 2 UART connections (excluding the USB port serial)
2. The ESP32 fully handles the open challenge, which requires just the right and left LiDAR. For the obstacle challenge, it merely acts as a node between the sensors and the Raspberry Pi. The third TF Luna is directly connected to the Raspberry Pi.

### Code Snippets for Components
#### Running 2 TF Luna Sensors with an ESP32 Devkit
```
// Program to get data from 2 TF-Luna LiDAR sensors connected to the ESP32 via UART connections

HardwareSerial tfLuna1(1);
HardwareSerial tfLuna2(2);

void setup() {
  Serial.begin(115200);
  delay(500);

  tfLuna1.begin(115200, SERIAL_8N1, 22, 23);
  tfLuna2.begin(115200, SERIAL_8N1, 19, 21);

  Serial.println("Setup Complete");
}

void readTFLuna(HardwareSerial &sensor, const char* label) {
  if (sensor.available()) {
    if (sensor.read() == 0x59) {
      if (sensor.read() == 0x59) {
        byte low = sensor.read();
        byte high = sensor.read();
        int distance = (high << 8) + low;

        sensor.read();
        sensor.read();
        sensor.read();
        sensor.read();
        sensor.read();

        Serial.print(label);
        Serial.print(" Distance: ");
        Serial.print(distance);
        Serial.println(" cm");
      }
    }
  }
}

void loop() {
  readTFLuna(tfLuna1, "Sensor 1");
  readTFLuna(tfLuna2, "Sensor 2");
}
```

#### Running the BNO055 Orientation Sensor with an ESP32 Devkit
```
// Program for running the BNO055 IMU sensor connected to an ESP32 devkit [on SDA pin 32 and SCL pin 33]

#include <Wire.h>
#include <Adafruit_Sensor.h>
#include <Adafruit_BNO055.h>
#include <utility/imumaths.h>

TwoWire myWire = TwoWire(0);
Adafruit_BNO055 bno = Adafruit_BNO055(55, 0x28, &myWire);

void setup() {
  Serial.begin(115200);
  myWire.begin(32, 33);

  if (!bno.begin()) {
    Serial.println("Error - BNO055 not detected");
    while (1);
  }

  delay(1000);
  bno.setExtCrystalUse(true);
  Serial.println("BNO055 initialized");
}

void loop() {
  sensors_event_t orientationData;
  bno.getEvent(&orientationData, Adafruit_BNO055::VECTOR_EULER);

  Serial.print("Yaw: ");
  Serial.print(orientationData.orientation.x);
  Serial.print(" | Roll: ");
  Serial.print(orientationData.orientation.y);
  Serial.print(" | Pitch: ");
  Serial.println(orientationData.orientation.z);

  delay(500);
}
```

#### Running a TF Luna with Raspberry Pi 5
```
import serial
import time

ser = serial.Serial(
    port="/dev/serial0",
    baudrate=115200,
    timeout=1
)

def read_lidar():
    while True:
        if ser.read() == b'\x59':
            if ser.read() == b'\x59':
                frame = ser.read(7)
                if len(frame) == 7:
                    distance = frame[0] + (frame[1] << 8)
                    strength = frame[2] + (frame[3] << 8)
                    temperature = (frame[4] + (frame[5] << 8)) / 8 - 256
                    checksum = frame[6]
                    checksum_calc = (0x59 + 0x59 + sum(frame[:6])) & 0xFF
                    if checksum_calc == checksum:
                        return distance, strength, temperature

if __name__ == "__main__":
    try:
        while True:
            result = read_lidar()
            if result:
                distance, strength, temperature = result
                print(f"Distance: {distance} cm | Strength: {strength} | Temp: {temperature:.1f}°C")
            time.sleep(0.1)
    except KeyboardInterrupt:
        ser.close()
        print("Stopped.")
```

### Problems We Faced and How We Solved Them
<ol>
<li>
<strong>Raspberry Pi Power Issues</strong>

At first, we were using the Li-ion battery to power the Raspberry Pi. We faced 2 issues in this.

Firstly, the Li-ion battery didn't give a proper constant output. There were a lot of voltage spikes and drops. This caused the Raspberry Pi to shut down in the middle of running. To fix this, we stopped powering the Raspberry Pi from the pins but instead gave it power through the USB-C port. This is because the USB-C port has built-in protection circuitry

Next, another problem we faced was the the Pi didn't receive enough current. We are using 2C 3.7v 2200mAh cells, which create a 2C 11.1v 2200mAh battery. 2.2 Ah * 2C = 4.4 Ah. The Raspberry Pi needs 5 Amps, and a lot of current is also consumed by the motors and other components. The 4.4 Amp battery was working fine we started running the motors. After that, the Pi gave a low voltage warning and soon shut down.

After that, we used a power bank. The problem with it was that was that it had a 5V 3A output, which was enough was a Raspberry Pi 4 but not for a Raspberry Pi 5

Finally, we settled on LiPo battery. This battery had a 2500 mAh capacity with a 3C discharge rate. This allowed for a maximum current of 7.5A. This battery is only used for the Raspberry Pi so that there are no voltage drops due to the motor or other components.
</li>

<li>
<strong>4 TF Luna sensors not working on ESP32</strong>
At first, we tried to connect all the TF Luna sensors to the ESP32. This did not work because the ESP32 only support 2 UART connections (excluding the USB bort Serial). To counter this problem, we connected the front sensors to the Raspberry Pi. This would not cause any issues at all since the front sensors aren't needed for the open challenge (the open challenge is fully run by the ESP32).
</li>
</ol>

### Potential Improvements
<ol>
<li><strong>Using a sing LiPo Battery Instead of Li-Ion and LiPo</strong>: We can use a different LiPo battery with a capacity of ~3000 mAh and a discahrge rate of 5C+. This will remove the need for the Li-ion battery.</li>
<br>
<li><strong>Using a Supercapacitor Buffer</strong>: This will stabilize and smooth out the output from the battery. It will smooth out voltage spikes and dips when motors suddenly draw high current, protecting the components</li>
<br>
<li><strong>Using Quaternion Angle Outputs on BNO055</strong>: The Euler angle outputs on the BNO055 orientation sensor don't work properly. When other axes are tilted beyond 20 degrees, the x axis value becomes unreliable and distorted. Using the quaternion values will require more code and conversions, but will be more reliable and precise. The problem within the sensor is that its internal firmware (version 0x0311) has a math bug.</li>
<br>
<li><strong>Using two BNO055 sensors</strong>: The BNO055 sometimes drifts over periods of extended use. To decrease the drift, we can use 2 sensors and average out the values to get a more accurate value</li>
<br>
</ol>

## Obstacle Management
### Open Challenge
The process for the open challenge is fairly simple. It is fully explained through the flowchart below.

<table>
  <tr>
    <td width="50%" style="text-align: left;">
      Open Challenge Flowchart
    </td>
  </tr>
</table>

### Obstacle Challenge
<table>
  <tr>
    <td width="50%" style="text-align: left;">
      Obstacle Challenge Flowchart
    </td>
  </tr>
</table>

#### Block Avoid Sequence
<table>
  <tr>
    <td width="500px" style="text-align: left;">
      Block Avoid Flowchart
    </td>
  </tr>
</table>

#### Failsafe Sequence
<table>
  <tr>
    <td width="500px" style="text-align: left;">
      Failsafe Sequence Flowchart
    </td>
  </tr>
</table>

### Block Detection
To detect the blocks, we are running OpenCV on the Raspberry Pi. The block detection is using masking with LAB color ranges. We chose the LAB color space instead of HSV or BGR because LAB is more reliable in different lighting.

LAB Color Space

### ESP32-Rasberry Pi Communication
Data sent from RPi to ESP32

Data Sent from ESP32 to RPi

### Code Snippet for Detecting Blocks
```
import cv2
import numpy as np
import time

def detect_biggest_block(frame, SHOW=False):
    global last_turn, DIRECTION
    full_h, full_w, _ = frame.shape
    roi_start = int(full_h * 0.2)
    frame = frame[roi_start:full_h, 0:full_w]

    adjusted = cv2.convertScaleAbs(frame, alpha=CONTRAST, beta=BRIGHTNESS)
    inv_gamma = 1.0 / GAMMA
    table = np.array([(i / 255.0) ** inv_gamma * 255 for i in np.arange(256)]).astype("uint8")
    adjusted = cv2.LUT(adjusted, table)

    lab = cv2.cvtColor(adjusted, cv2.COLOR_BGR2LAB)
    l, a, b = cv2.split(lab)
    clahe = cv2.createCLAHE(clipLimit=2.0, tileGridSize=(8, 8))
    l_clahe = clahe.apply(l)
    lab_clahe = cv2.merge((l_clahe, a, b))
    adjusted_frame = cv2.cvtColor(lab_clahe, cv2.COLOR_LAB2BGR)

    lab_frame = cv2.cvtColor(adjusted_frame, cv2.COLOR_BGR2LAB)
    lab_raw = cv2.cvtColor(frame, cv2.COLOR_BGR2LAB)

    detections = {"red": [], "green": [], "blue": [], "orange": []}
    blue_y_values, orange_y_values = [], []

    for color, (lower, upper) in COLOR_RANGES.items():
        lower_bound = np.array(lower, dtype=np.uint8)
        upper_bound = np.array(upper, dtype=np.uint8)
        source_lab = lab_raw if color == "orange" else lab_frame
        mask = cv2.inRange(source_lab, lower_bound, upper_bound)

        kernel = np.ones((3, 3), np.uint8)
        mask = cv2.morphologyEx(mask, cv2.MORPH_OPEN, kernel, iterations=2)
        mask = cv2.morphologyEx(mask, cv2.MORPH_CLOSE, kernel, iterations=2)

        contours, _ = cv2.findContours(mask, cv2.RETR_EXTERNAL, cv2.CHAIN_APPROX_SIMPLE)
        for cnt in contours:
            area = cv2.contourArea(cnt)
            if area < MIN_AREA.get(color, 0):
                continue
            x, y, w_box, h_box = cv2.boundingRect(cnt)
            cx, cy = x + w_box // 2, y + h_box // 2
            detections[color].append((cx, cy, area, color))
            if color == "blue":
                blue_y_values.append(cy)
            elif color == "orange":
                orange_y_values.append(cy)

            if SHOW:
                cv2.rectangle(frame, (x, y), (x + w_box, y + h_box), colors[color], 2)
                cv2.circle(frame, (cx, cy), 4, colors[color], -1)
                cv2.putText(frame, f"{color} ({area})", (x, y - 10),
                            cv2.FONT_HERSHEY_SIMPLEX, 0.6, colors[color], 2)

    max_blue_y = max(blue_y_values) if blue_y_values else None
    max_orange_y = max(orange_y_values) if orange_y_values else None

    valid_blocks = []
    for color in ["red", "green"]:
        for (cx, cy, area, col) in detections[color]:
            if time.time() - last_turn > COOLDOWN:
                if max_blue_y and cy <= max_blue_y:
                    continue
                if max_orange_y and cy <= max_orange_y:
                    continue
            valid_blocks.append((col, cy, cx, area))

    closest_block = None
    if valid_blocks:
        closest_block = max(valid_blocks, key=lambda b: b[1])
        color, cy, cx, area = closest_block
        cy_full = cy + roi_start
        x_percent = (cx / full_w) * 100
        y_percent = ((full_h - cy_full) / full_h) * 100
        cell_w = full_w // 5
        cell_h = full_h // 5
        col_idx = cx // cell_w
        row_idx = cy_full // cell_h
        cell_number = row_idx * 5 + col_idx + 1
    else:
        color, cy, cx, area, cell_number, x_percent, y_percent = (None, None, None, None, None, None, None)

    if SHOW:
        cell_w = full_w // 5
        cell_h = full_h // 5
        display = frame.copy()
        for i in range(1, 5):
            cv2.line(display, (i * cell_w, 0), (i * cell_w, frame.shape[0]), (200, 200, 200), 1)
        for j in range(1, 5):
            y_line = j * cell_h - roi_start
            if 0 <= y_line < frame.shape[0]:
                cv2.line(display, (0, y_line), (frame.shape[1], y_line), (200, 200, 200), 1)
        num = 1
        for r in range(5):
            for c in range(5):
                y_pos = r * cell_h + 20 - roi_start
                if 0 <= y_pos < frame.shape[0]:
                    x_pos = c * cell_w + 10
                    cv2.putText(display, str(num), (x_pos, y_pos),
                                cv2.FONT_HERSHEY_SIMPLEX, 0.5, (180, 180, 180), 1)
                num += 1
        if closest_block:
            cv2.rectangle(display, (cx - 20, cy - 20), (cx + 20, cy + 20), (0, 255, 255), 3)
            cv2.putText(display, f"Closest: {color} Cell:{cell_number}",
                        (cx, cy - 30), cv2.FONT_HERSHEY_SIMPLEX, 0.7, (0, 255, 255), 2)
        cv2.imshow("Block Detection", display)
        cv2.waitKey(1)

    return (color if closest_block else None,
            y_percent if closest_block else None,
            x_percent if closest_block else None,
            area if closest_block else None,
            cell_number if closest_block else None)
```

### Code Snippet for Moving Straight with KP
```
// Driving in a straight line

// Including Libraries
#include <Wire.h>
#include <Adafruit_Sensor.h>
#include <Adafruit_BNO055.h>
#include <utility/imumaths.h>

// Defining Pins
#define IN1 13
#define IN2 12
#define ENA 14

// Setting Up Communication with BNO055
TwoWire myWire = TwoWire(0);
Adafruit_BNO055 bno = Adafruit_BNO055(55, 0x28, &myWire);

// Settings Variables
const float target_direction = 0;
const float kp = -1; // Robot will move in opposite direction of the error

const int servoPin = 25;
const int servoCenter = 95; // Servo position at which the steering system is centered

// Custom function to rotate the servo (the default PWM of the ESP32 is unreliable)
void moveServoAngle(int angle){
  angle = constrain(angle,0,180);
  int pulsewidth = map(angle,0,180,500,2400);
  digitalWrite(servoPin, HIGH);
  delayMicroseconds(pulsewidth);
  digitalWrite(servoPin, LOW);
  delay(20 - pulsewidth/1000);
}

// Steer function to automatically account for servo center when called
void steer(int direction)
{
  moveServoAngle(servoCenter + direction);
}

void setup(void) 
{
  Serial.begin(115200);

  pinMode(servoPin, OUTPUT);

  pinMode(IN1, OUTPUT);
  pinMode(IN2, OUTPUT);
  pinMode(ENA, OUTPUT);
  
  steer(0);

  myWire.begin(32, 33);

  if(!bno.begin())
  {
    Serial.println("No BNO055 detected ... Check your wiring or I2C ADDR!");
    while(1);
  }

  delay(2000); 
  bno.setExtCrystalUse(true);
}

void loop(void) 
{
  digitalWrite(IN1, HIGH);
  digitalWrite(IN2, LOW);
  analogWrite(ENA, 200);
  sensors_event_t orientationData;
  bno.getEvent(&orientationData, Adafruit_BNO055::VECTOR_EULER);
  float direction = orientationData.orientation.x;
  if (direction > 180)
  {
    direction -= 360; // Normalizes angle from 0 to 360 to -180 to 180 where 0 is front, -90 is left and 90 is right
  }

  float error = direction - target_direction;
  int steer_val = (int) error*kp; // Calculate Correction Required

  steer_val = constrain(steer_val, -40, 40);

  Serial.print("Steer: ");
  Serial.println(steer_val);
  steer(steer_val);
}
```

### Code Snippet for Wall Following in one direction (Clockwise) (For Open Challenge)
Check out [this](#running-2-tf-luna-sensors-with-an-esp32-devkit), [this](#running-the-bno055-orientation-sensor-with-an-esp32-devkit), and [this](#running-the-mg90-servo-motor-with-an-esp32-devkit) for definitions of functions called in the code below
```
void loop(void) {
  updateTFLuna(Serial1, distance_right);

  if (counter < 12) {
    digitalWrite(IN1, HIGH);
    digitalWrite(IN2, LOW);
    analogWrite(ENA, 255);

    sensors_event_t orientationData;
    bno.getEvent(&orientationData, Adafruit_BNO055::VECTOR_EULER);
    float heading = normalizeAngle(orientationData.orientation.x);

    float error = normalizeAngle(heading - target_direction);
    int steer_val = (int)(error * kp);
    steer_val = constrain(steer_val, -40, 40);
    steer(steer_val);

    if (distance_right >= 50) {
      target_direction += 90;
      target_direction = normalizeAngle(target_direction);

      while (true) {
        updateTFLuna(Serial1, distance_right);
        bno.getEvent(&orientationData, Adafruit_BNO055::VECTOR_EULER);
        heading = normalizeAngle(orientationData.orientation.x);
        error = normalizeAngle(heading - target_direction);
        steer_val = (int)(error * kp);
        steer_val = constrain(steer_val, -40, 40);
        steer(steer_val);
        digitalWrite(IN1, HIGH);
        digitalWrite(IN2, LOW);
        analogWrite(ENA, 250);
        if (abs(error) <= 10) break;
      }

      counter++;
      steer(0);
      digitalWrite(IN1, HIGH);
      digitalWrite(IN2, LOW);
      analogWrite(ENA, 250);
      delay(500);

      while (true) {
        updateTFLuna(Serial1, distance_right);
        if (distance_right < 50 && distance_right > 0) break;
        delay(10);
      }
    }
  }

  else {
    digitalWrite(IN1, HIGH);
    digitalWrite(IN2, LOW);
    analogWrite(ENA, 255);
    delay(200);
    digitalWrite(IN1, LOW);
    digitalWrite(IN2, LOW);
    analogWrite(ENA, 0);
    while (1); // Stay stopped
  }
}
```

The full source code of the robot is provided [here](https://github.com/WRO-Team-TheStatesmen/wro2025-fe-statesmen/tree/main/src)

### Problems We Faced and How We Solved Them
<ol>
<li><strong>Block not Being Detected in Different Lighting Conditions</strong>
At first, we were using HSV ranges. A major problem with them was they were extremely unreliable. They caused a lot of noise and didn't work if the lighting changed.
<br><br>
To fix this, we used the LAB color space. This works better with different lighting conditions. You can see about it
</li>

[here](#block-detection)

<br>
<li>
<strong>Colliding into blocks</strong>
Another major problem was that it was often colliding into the traffic signs as it avoided them. This was when there when a block was placed right after a turn.
<br><br>
To fix this, we added a reverse failsafe. We basically made it so that if the block was right in front of the robot, the robot would reverse and then continue.
</li>
</ol>

### Potential Improvements
<ol>
<li><strong>Using a 360° LiDAR Sensor</strong>: Our current TF Luna LiDAR sensors can only see in 1 direction. If we use a 360° LiDAR sensor, the robot will be able to see everything around it, which can significantly improve its performance.</li>
<br>
<li><strong>Using ROS2</strong>: Using the Robot Operation System 2 (ROS2) would be much better. This OS is custom-made for robots and has a lot of features. Using this will improve the performance of the robot.</li>
<br>
<li><strong>Using PID</strong>: We are currently using just KP to move straight. It would be better if we implement the full PID algorithm (KP, KI, and KD). This will make the robot movements smoother</li>
</ol>

## Engineering Factor
As shown in the previous sections, we have used our own design for the vehicle. We have also used off the shelf electrical components such as motors and sensors.

## Software Integration
Our robot relies not only on the hardware, but our seamless integration of our software with every single component. We have made a modular software architecture that separates low-level hardware control, communication protocols, and high-level decision-making

Software Integration Flowchart

### System Architecture
The ESP32 acts as a hub between the Raspberry Pi and the motor, servo motor, the BNO055 orientation sensor and 2 LiDAR sensors. The ESP32 is connected to these components. It is only reponsible for sending data to and receiving data from them. It acts as a hub in the middle.

ESP32 Integration with Components

The Raspberry Pi is the brain of our robot. It is responsible for image processing and making decisions. It is also connected to the front LiDAR sensor because the ESP32 can only handle 2 UART connections.

Raspberry Pi Integration with Components

### Communication Protocol
The Raspberry Pi needs to have all the data to make proper decisions. It needs data recorded by the ESP32 for that. For this, we have created a csv-based serial communication system between the Raspberry Pi and ESP32.

The Raspberry Pi is connected to the ESP32 via a USB cable. The ESP32 sends the data to the Raspberry Pi over a serial connection at a baud rate of 115200, which means 115200 signal changes per second.

The ESP32 sends 3 values to the ESP32:

| Data Value 1 | Data Value 2 | Data Value 3 |
|---|---|---|
| BNO055 Heading (*Orientation.x*) | Left Distance from TF Luna | Right Distance from TF Luna |

Data Sent from ESP32 to RPi

After the ESP32 receives all the data, it processes it. It detects the location of the block and based on that it decides where the robot should go. For that, it needs to send the data to the ESP32. The Raspberry Pi sends 3 values to the ESP32.

| Data Value 1 | Data Value 2 | Data Value 3 |
|---|---|---|
| Speed | Movement Direction (Front/Back) | Steer Angle |

Data sent from RPi to ESP32

#### Error Checks
In data communication, there is also a small chance of errors. To prevent this, whenever data is received it is checked for errors.

1. If more than 3 data values are received, then that whole piece of data is discarded and considered having errors

2. If the data values received contain characters other that numbers, the data is discarded and considered having errors

3. If the value of the data exceeds the bounds, the data is discarded and considered having errors

#### Error Checking for Data Received by ESP32
Error Checking ESP32

#### Error Checking for Data Received by ESP32
Error Checking RPi

### Code Modularity (Hardware Abstraction Layer)
We have structured our code in a modular way. Each component of the robot is handled by a dedicated function. This ensures that our script remains easily understandable and changes can be made without any trouble. The code can also easily be understood and reused

#### Function for TF Luna
```
void updateTFLuna(HardwareSerial &sensor, volatile int &distanceVar) {
  while (sensor.available() >= 9) {
    if (sensor.read() == 0x59 && sensor.read() == 0x59) {
      byte low = sensor.read();
      byte high = sensor.read();
      int distance = (high << 8) + low;

      for (int i = 0; i < 5; i++) sensor.read();

      if (distance <= 500)
      {
        distanceVar = distance;
      }
    }
  }
}
```

This function works in a special way. Instead of returning a value, this function updates a global variable. This way, we can make sure that the program doesn't slow down as the clock speed of the TF Luna and the ESP32 is different. Earlier, it was slowing down is it waited until the TF Luna sent a value. Now, it only updates the variable when the TF Luna sends a value.

#### Function for BNO055
```
void updateBNO055(Adafruit_BNO055 &bno, volatile float &headingVar) {
  sensors_event_t orientationData;
  bno.getEvent(&orientationData, Adafruit_BNO055::VECTOR_EULER);
  headingVar = orientationData.orientation.x;
}
```

This function works in the same way as the `updateTFLuna()` function

#### Function for Motor
```
void setMotor(int speed, int direction) {
  speed = constrain(speed, 0, 255);

  if (direction == 0) {  
    digitalWrite(IN1, HIGH);
    digitalWrite(IN2, LOW);
  }
  else if (direction == 1) {  
    digitalWrite(IN1, LOW);
    digitalWrite(IN2, HIGH);
  }

  analogWrite(ENA, speed);
}
```

#### Function for Servo Motor
```
void moveServoAngle(int angle) {
  angle = constrain(angle, 0, 180);
  int pulsewidth = map(angle, 0, 180, 500, 2400);
  digitalWrite(servoPin, HIGH);
  delayMicroseconds(pulsewidth);
  digitalWrite(servoPin, LOW);
  delay(20 - pulsewidth / 1000);
}

void steer(int angleOffset) {
  moveServoAngle(servoCenter + angleOffset);
}
```

To control our steering system from the MG90 servo motor, we created 2 functions.

`moveServoAngle()` is a low-level function that sends a PWM signal. We used this instead of ledcWrite because of 3 main reasons
1. ledcWrite is unreliable
2. Precise control over pulse width
3. Modularity and clarity

`steer()` is a high-level function. This lets us directly decide what direction the robot goes in. It automatically accounts for the center position of the servo motor. If we put the value 0, the robot travels straight, + means right, and - means left.

#### Function for LiDAR Sensor (Raspberry Pi)
```
def get_front(port="/dev/ttyAMA0", baud=115200, timeout=0.1):
    try:
        with serial.Serial(port, baud, timeout=timeout) as ser:
            frame = ser.read(9)
            if len(frame) != 9:
                return None

            if frame[0] != 0x59 or frame[1] != 0x59:
                return None

            dist = frame[2] | (frame[3] << 8)
            return dist if dist >= 0 else None
    except serial.SerialException as e:
        return None
```

### Communication API (Communication Layer)
We created specialized python functions to have a communication system which can be debugged, edited, and understood easily

#### readData()
```
def read_data(DEBUG: bool = False):
    try:
        line = ser.readline().decode(errors="ignore").strip()
        if not line:
            if DEBUG:
                print("No data received from serial.")
            return None, None, None, None

        parts = line.split(",")
        if len(parts) != 3:
            if DEBUG:
                print(f"Invalid data format: {line}")
            return None, None, None, None

        angle = normalize_angle(int(parts[0]))
        left = int(parts[1])
        right = int(parts[2])

        front = get_front(port=LIDAR_PORT) if DIRECTION else 100 # A default value of 100 is returned if the robot does not know the direction yet to avoid errors

        if DEBUG:
            print(f"Read -> Angle: {angle}, Left: {left}, Front: {front}, Right: {right}")

        return angle, left, front, right

    except (ValueError, UnicodeDecodeError) as e:
        if DEBUG:
            print(f"Data parsing error: {e}")
        return None, None, None, None
    except Exception as e:
        if DEBUG:
            print(f"Unexpected error in read_data: {e}")
        return None, None, None, None
```

This function is used to read the incoming data from the ESP32. It will be run on the Raspberry Pi.

#### sendData()
```
def send_data(speed, direction, steer, DEBUG=False):
    cmd = f"{speed},{direction},{steer}\n"
    if DEBUG:
      print(f"Data Sent: {cmd}")
    ser.write(cmd.encode())
```

This function is used to send the speed, movement direction (front or back), and steer angle to the ESP32. Once the raspberry pi makes a decision, it can use this function to send that decision.

### Debugging
Throughout development, there were multiple challenges in the hardware-software integration, such as incorrect sensor readings, communication errors, etc. To address these issues, we created a structured debugging process.

#### Component Debugging (Unit Testing)
If there is a problem in any single component, we have a way of debuggin that as well. You can see [here](/src/invididual-components/) that we have individual programs to test out individual components. With this, we can know exactly what problem is being faced.

#### Communication Debugging (Integration Testing)
We implemented debugging tools directly within our code. As you can see in the `readData()` and `sendData()` functions, there is a DEBUG parameter. If this parameter is set to `True`, then whatever data is being sent / received will be printed. This makes debugging extremely easy.

Also, there is another way of checking communication on the ESP32 end. The ESP32 can directly be connected to a laptop. Then, the Arduino IDE can be opened. Since the data is sent via serial in csv format, it can easily be seen through the serial monitor. We can also send data easily via the serial monitor to the ESP32

Error Checking RPi

To easily be able to send data to the ESP32 without using the serial monitor, we createed a custom python program with `pygame` to control the robot

You can see the code of the program [here](/src/tools/pygame-debugging.py)

Pygame Debugging

#### Image Processing Debugging
Also, we made it so that when the robot is running, we can connect to the Raspberry Pi via VNC and see the live camera feed. This camera feed will show all the blocks detected and how the robot is taking decisions. You can view it [here](/other/README-images/SoftwareIntegration/Debugging.mp4)

## Robot Construction Guide
### Step 1 - Print the Parts
Firstly, you will need to print all the parts. The *.STL files to be printed are [here](https://github.com/WRO-Team-TheStatesmen/wro2025-fe-statesmen/tree/main/models). We used the Bambu Lab X1-Carbon 3D printer to print everything.

### Step 2 - Assemble the Chassis
Next, you will need to assemble the chassis. The guide to assemble the chassis is given [here](https://github.com/WRO-Team-TheStatesmen/wro2025-fe-statesmen/blob/main/other/README-images/Chassis/ChassisAssembly.pdf). We have used lego parts for the chassis to make it so that we can easily change it.

### Step 3 - Attach the Components
<strong>Step 1 - Insert the batteries in the chassis in the section shown below</strong>

Step 3 - 1

You may secure the batteries using double sided tape

<strong>Step 2 - Screw the TF Luna LiDAR sensors to the 3D printed mounts and attach those mounts to the chassis as shown below</strong>

TF Luna 1 (Left)

Step 3 - 2 - 1

TF Luna 2 (Right)

Step 3 - 2 - 2

TF Luna 3 (Front)

Step 3 - 2 - 3

For the front TF Luna, you will have to attach a 5-hole beam to the marked place and then attach the mount to that beam

<strong>Step 3 - Insert the Raspberry Pi in the chassis as shown below</strong>

Step 3 - 3

<strong>Step 4 - Place the PCB with the ESP32, BNO055, LM2596, and other connections on the section shown below</strong>

Step 3 - 4

### Step 4 - Connect the Components
Connect all the components with each other as per the electrical diagrams in above sections

### Step 5 - Upload the Code to the ESP32
Open the /src/final-code/ folder in the GitHub directory. Depending on if you want to run the open challenge or the obstacle challenge, open the respective directory. In that directory there will be 1 or 2 files. The will be a *.ino file and a *.py file (only for obstacle challenge). Download the files.

Open the *.ino file in the Arduino IDE. Connect the ESP32 to the device. Click on "choose board and port" and choose the "DOIT ESP32 Devkit v1" board in the boards section and the correct COM port in the "ports" section

Then, click on the upload code button to upload the code to the ESP32

### Step 6 - Set Up the Raspberry Pi
Next, you will need up to set up a Raspberry Pi

Step 1 - Install Raspbian OS on an SD card
<ol>
<li>Get a micro SD card (recommended 32 GB) and put it into your device (you may require a micro SD card adapter)</li>
<li>Install the <a href="https://www.raspberrypi.com/software/">Raspberry Pi imager</a></li>
<li>Open the software, choose your micro SD card, and flash the Raspbian OS (64 bit) into the SD card</li>
</ol>

Step 2 - Turn on the Raspberry Pi
<ol>
<li>Insert the micro SD card into the Raspberry Pi</li>
<li>Connect the Raspberry Pi to a screen</li>
<li>Power the Raspberry Pi (preferably using the official adapter)</li>
</ol>

Step 3 - Set up the Raspberry Pi
<ol>
<li>Follow the configuration steps on the screen</li>
<li>Open the terminal</li>
<li>Enter the command <code>sudo apt update</code></li>
<li>Enter the command <code>sudo apt upgrade</code></li>
<li>Enter the command <code>sudo raspi-config</code> and then go to interface options > UART > enable</li>
</ol>

Step 4 - Install the required libraries and code
<ol>
<li>Go into the desktop using this command: <code>cd Desktop</code></li>
<li>Clone the GitHub repository using this command: <code>git clone https://github.com/WRO-Team-TheStatesmen/wro2025-fe-statesmen.git</code></li>
<li>Create a virtual environment using this command: <code>python3 -m venv venv</code></li>
<li>Download the required libraries using this command: <code>./venv/bin/python3 -m pip install opencv-python pyserial numpy</code></li>
</ol>

### Step 8 - Run the Code
To run the code on the Raspberry Pi, all you need to do is run the command `./venv/bin/python3 ./src/final-code/obstacle-challenge/obstacle-challenge.py`

## The Challenge
You can view the challenge rules [here](https://wroindia.org/wp-content/uploads/2025/01/WRO-2025-Future-Engineers-Self-Driving-Cars-General-Rules.pdf)

You can find the playfield [here](https://wroindia.org/wp-content/uploads/2025/01/WRO-2025_FutureEngineers_Playfield-1.pdf)

## Randomizer
We also made a randomizer for automatically setting up a randomization. You can view it [here](/other/obstacle-randomizer.zip)

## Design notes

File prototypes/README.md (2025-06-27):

# Prototypes
This directory contains the documentation of the prototypes built.

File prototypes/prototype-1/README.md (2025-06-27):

# Prototype 1
This directory contains the documentation of the first prototype we built.

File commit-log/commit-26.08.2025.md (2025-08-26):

# Commit - 26 August 2025
This commit adds the 3D models for the servo mount

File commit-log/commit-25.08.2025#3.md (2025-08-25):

# Commit - 25 August 2025 \# 3
This commit adds a pdf for the assembly instructions for the chassis

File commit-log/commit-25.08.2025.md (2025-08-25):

# Commit - 25 August 2025
This commit adds the 3d models for the servo-axle adapter, motor-axle adapter, and TF Luna mount.

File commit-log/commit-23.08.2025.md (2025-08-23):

# Commit - 23 August 2025
This commit adds a program for anticlockwise wall following and also updates the code for clockwise wall following (the servo center is changed to 90)

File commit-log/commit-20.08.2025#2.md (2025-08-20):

# Commit - 20 August 2025 \#2
This commit adds python scripts for some tools.
1. Camera Settings - This is to adjust the camera settings like brightness, contrast, and gamma
2. HSV Calibration - The video capture camera number is updated
3. RGB Calibration - The video capture camera number is updated
4. LAB Calibration - A program is added for calibrating a mask in the LAB color space

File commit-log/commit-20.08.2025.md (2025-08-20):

# Commit - 20 August 2025
This commit updates the ESP32 and RPI communication protocol. Now, there is an ultrarsonic sensor for the front and also an IR sensor.
5 values are sent from the ESP32 to the Raspberry Pi:
1. Angle (BNO055)
2. Left Distance (TF Luna)
3. Front Distance (Ultrasonic)
4. Right Distance (TF Luna)
5. IR Value (0 or 1)

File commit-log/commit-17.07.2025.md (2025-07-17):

# Commit - 17 July 2025
This commit adds a program for centering the servo motor. This will help when adjusting prototype structure. There is also a minor change in the steering-driving script - the servo center is adjusted.

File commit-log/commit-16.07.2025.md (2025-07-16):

# Commit - 16 July 2025
This commit adds a program for communication between ESP32 and Raspberry Pi

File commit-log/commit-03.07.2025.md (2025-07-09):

# Commit - 3 July 2025
This commit adds python programs for calibrating upper and lower limits of RGB and HSV values for block detection.

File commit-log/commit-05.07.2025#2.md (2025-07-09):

# Commit - 5 July 2025 \#2
This commit adds a 3d model for the servo mount.

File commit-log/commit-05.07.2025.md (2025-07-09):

# Commit - 5 July 2025
This commit adds print commands at the end of the RGB and HSV calibration python programs.

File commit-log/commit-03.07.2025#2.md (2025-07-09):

# Commit - 27 June 2025 \#2
This commit adds a 3d model for the servo mount.

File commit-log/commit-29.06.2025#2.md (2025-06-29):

# Commit - 29 June 2025 \#2
This commit adds the program for wall following with an ESP32. The program works on prototype 1.
The grammar of the log of the previous commit is fixed.

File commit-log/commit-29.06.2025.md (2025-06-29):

# Commit - 29 June 2025
This commit adds the programs for driving while steering and driving in a straight line. Both of the programs work on prototype 1.

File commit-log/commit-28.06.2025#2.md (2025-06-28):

# Commit - 28 June 2025 \# 2
This commit adds the programs for the working of the TF-Luna LiDAR sensor and another program for the working of the MG90 servo motor (both with an ESP32 microcontroller on the prototype 1).
An additional comment is added in the /src/individual-components/servo-esp32-test/servo-esp32-test.ino file

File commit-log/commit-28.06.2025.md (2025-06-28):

# Commit - 28 June 2025
This commit adds the programs for the working of the BNO055 IMU sensor and another program for the working of the MG90 servo motor (both with an ESP32 microcontroller on the prototype 1).
The commit log file for the previous commit which was named incorrectly is renamed to the correct name as well.

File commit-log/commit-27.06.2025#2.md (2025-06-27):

# Commit - 27 June 2025 \#2
This commit updates the information about prototype 1, specifically the prototypes/prototype-1/prototype-1.md file.

There is also a minor change in the README.md file.

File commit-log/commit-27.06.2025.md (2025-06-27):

# Commit - 27 June 2025
This commit adds basic information about prototype 1.

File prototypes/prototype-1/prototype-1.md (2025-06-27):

# Prototype 1

## 1. Overview
We are building our first prototype out of lego parts to make changing the chassis easier. This prototype is primarily for the purpose of testing of components and systems as well as finding an optimized chassis design before building the final robot. It uses a single rear-wheel drive motor and a steering mechanism controlled by a servo motor. It has a parallel steering geometry.

## 2. Materials
The robot contains the following components:-
- 1x ESP32 Devkit
- 1x LM2596 Buck Convertor
- 1x 11.1v Li-ion Battery
- 1x BNO055 IMU Sensor
- 2x TF-Luna LiDAR Sensors
- 1x L293D Motor Driver IC
- 1x DC TT Motor (Yellow)
- 1x MG90 Servo Motor

## 3. Mechanical Design
- Real-wheel drive robot
- Parallel steering geometry with front wheels steered by an MG90 servo motor
- Rear wheels are powered by a DC motor
- LiDAR sensors on left and right side

## 4. Electronics, Wiring and Power
A perfboard is used on which the circuit connections have been made. An 11.1v Li-ion battery powers the robot. This battery is connected to a buck converter which converts it to 5v so that the ESP32 can be powered. The same 5v is given to the LiDAR sensors and servo motor. The ESP32 further powers the IMU with 3.3v.

## 5. Communication Overview
The two LiDAR sensors are connected to the ESP32 via UART connections. The BNO055 is connected to the ESP32 via an I2C conncetion. The ESP32 sends data to the L293D motor driver IC by digital outputs for direction, and a PWM output for speed control.

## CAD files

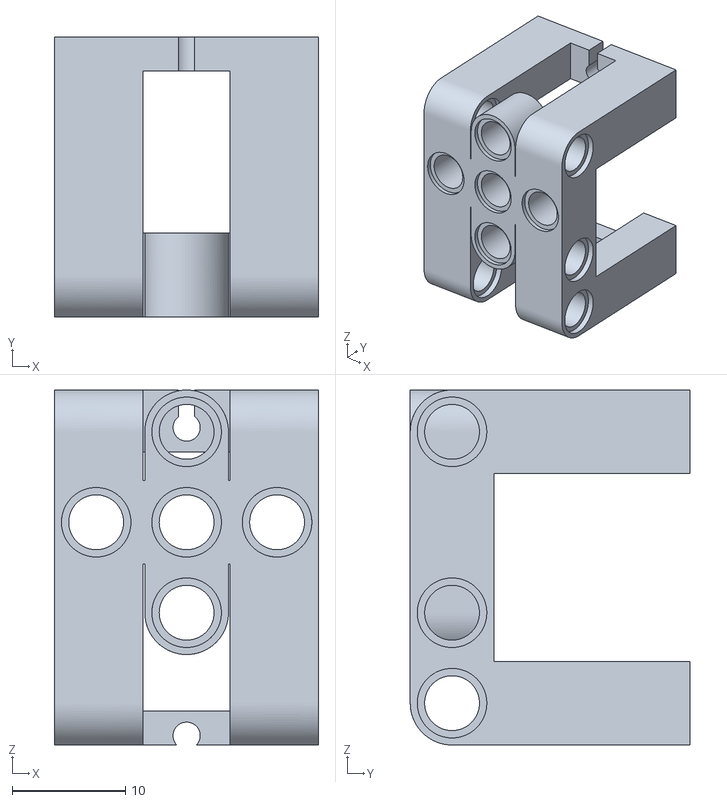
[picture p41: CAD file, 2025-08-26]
models/servo-mount-bottom.stl
23.4 x 24.7 x 31.4

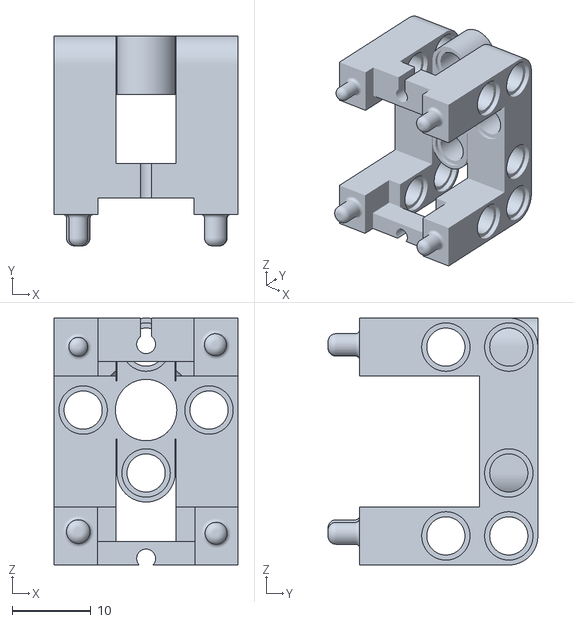
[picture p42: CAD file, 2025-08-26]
models/servo-mount-top.stl
23.4 x 26.7 x 31.4

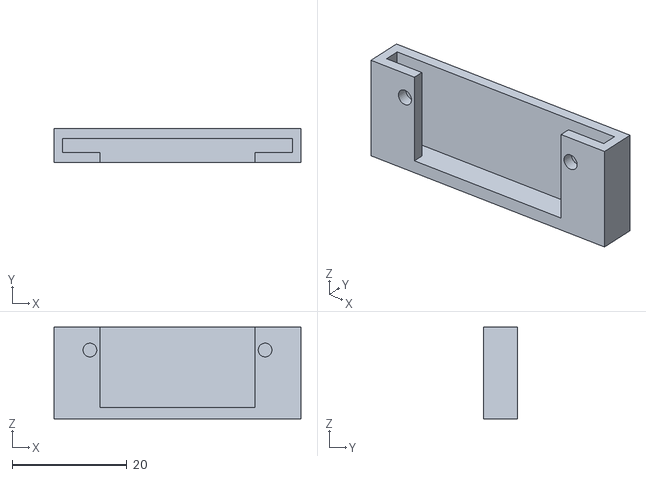
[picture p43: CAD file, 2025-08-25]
models/tf-luna-mount.stl
43.0 x 6.00 x 16.0

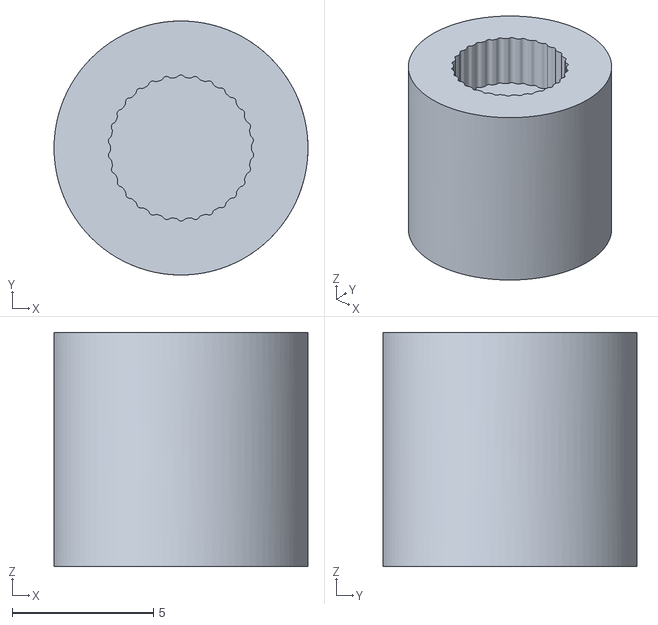
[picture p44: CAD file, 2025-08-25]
models/servo-axle-adapter.stl
9.00 x 9.00 x 8.30

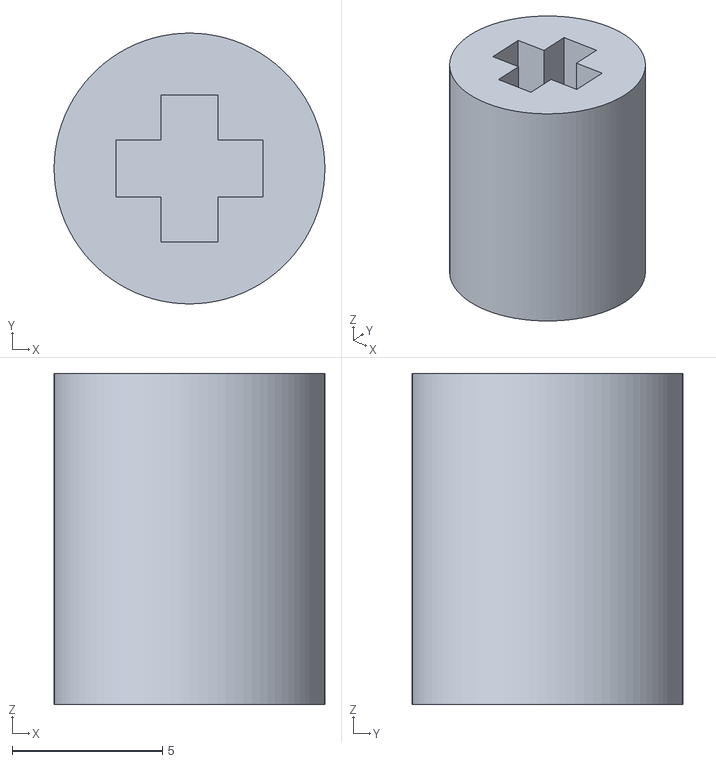
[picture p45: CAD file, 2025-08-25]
models/motor-axle-adapter.stl
9.00 x 9.00 x 11.0

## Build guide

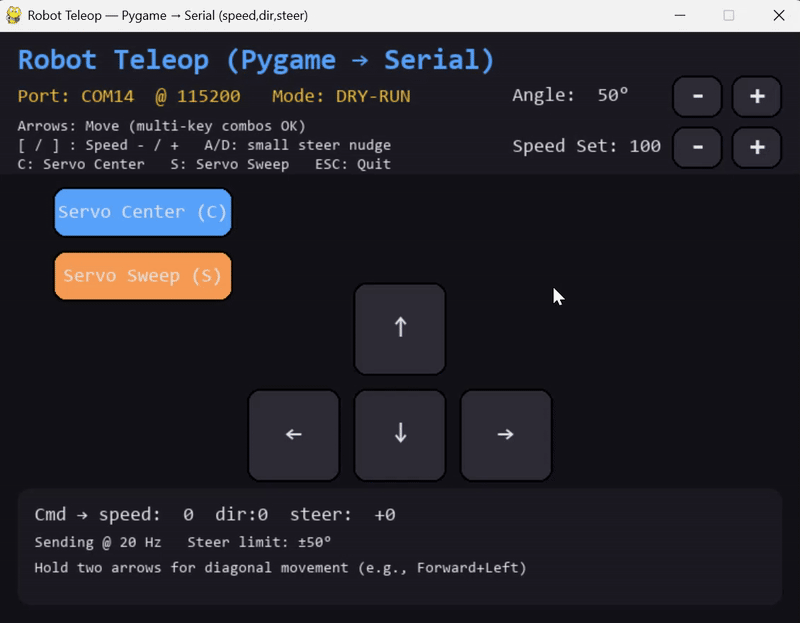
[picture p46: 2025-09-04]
other/README-images/SoftwareIntegration/pygame_tutorial.gif

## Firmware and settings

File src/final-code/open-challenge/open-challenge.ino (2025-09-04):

// Including Required Libraries
#include <Wire.h>
#include <Adafruit_Sensor.h>
#include <Adafruit_BNO055.h>
#include <utility/imumaths.h>

// Defining Pins
#define IN1 13
#define IN2 12
#define ENA 14

#define RXD1 22 // Right
#define TXD1 23
#define RXD2 19 // Left
#define TXD2 21

// Initiating the BNO055
TwoWire myWire = TwoWire(0);
Adafruit_BNO055 bno = Adafruit_BNO055(55, 0x28, &myWire);

// Defining Constants and Variables
int counter = 0;
int direction = 0; // 1 = clockwise, 2 = anticlockwise

const float kp = -1;
const int servoPin = 25;
const int servoCenter = 88;

float target_direction = 0.0;

volatile int distance_right = 0;
volatile int distance_left = 0;

const int button_pin = 3;

const int SPEED = 125;

// Defining Functions
float normalizeAngle(float angle) {
  while (angle > 180) angle -= 360;
  while (angle <= -180) angle += 360;
  return angle;
}

void moveServoAngle(int angle) {
  angle = constrain(angle, 0, 180);
  int pulsewidth = map(angle, 0, 180, 500, 2400);
  digitalWrite(servoPin, HIGH);
  delayMicroseconds(pulsewidth);
  digitalWrite(servoPin, LOW);
  delay(20 - pulsewidth / 1000);
}

void waitForOK() {
  Serial.println("Waiting for OK to start...");
  String input = "";
  while (true) {
    if (Serial.available()) {
      char c = Serial.read();
      if (c == '\n' || c == '\r') {
        input.trim();
        if (input.equalsIgnoreCase("OK")) {
          Serial.println("OK received. Starting...");
          break;
        }
        input = "";
      } else {
        input += c;
      }
    }
  }
}

void steer(int direction) {
  moveServoAngle(servoCenter + direction);
}

void updateTFLuna(HardwareSerial &sensor, volatile int &distanceVar) {
  while (sensor.available() >= 9) {
    if (sensor.read() == 0x59 && sensor.read() == 0x59) {
      byte low = sensor.read();
      byte high = sensor.read();
      int distance = (high << 8) + low;

      for (int i = 0; i < 5; i++) sensor.read();

      if (distance <= 500) {
        distanceVar = distance;
      }
    }
  }
}

// Setup
void setup(void) {
  Serial.begin(9600);
  Serial1.begin(115200, SERIAL_8N1, RXD1, TXD1); // Right LiDAR
  Serial2.begin(115200, SERIAL_8N1, RXD2, TXD2); // Left LiDAR

  pinMode(servoPin, OUTPUT);
  pinMode(IN1, OUTPUT);
  pinMode(IN2, OUTPUT);
  pinMode(ENA, OUTPUT);

  pinMode(button_pin, INPUT);

  steer(0);
  myWire.begin(32, 33);

  if (!bno.begin()) {
    while (1); // Halt if sensor fails to initialize
  }

  delay(2000);
  bno.setExtCrystalUse(true);
  Serial.println("DEBUG: SETUP COMPLETE (Detect direction then use one LiDAR)");

  // waitForOK();
  while (digitalRead(button_pin) == HIGH) {}
  Serial.println("Button clicked");
}

// Main Loop
void loop(void) {
  while (direction == 0) {
    updateTFLuna(Serial1, distance_right);
    updateTFLuna(Serial2, distance_left);

    digitalWrite(IN1, HIGH);
    digitalWrite(IN2, LOW);
    analogWrite(ENA, SPEED);

    Serial.print("Left: ");
    Serial.print(distance_left);
    Serial.print(" | Right: ");
    Serial.println(distance_right);

    sensors_event_t orientationData;
    bno.getEvent(&orientationData, Adafruit_BNO055::VECTOR_EULER);
    float heading = normalizeAngle(orientationData.orientation.x);

    float error = normalizeAngle(heading - target_direction);
    int steer_val = (int)(error * kp);
    steer_val = constrain(steer_val, -30, 30);
    steer(steer_val);

    if (distance_right >= 100) {
      direction = 1;
      Serial.println("Direction chosen: CLOCKWISE");
    } else if (distance_left >= 100) {
      direction = 2;
      Serial.println("Direction chosen: ANTICLOCKWISE");
    }
  }

  if (counter < 12) {
    digitalWrite(IN1, HIGH);
    digitalWrite(IN2, LOW);
    analogWrite(ENA, SPEED);

    sensors_event_t orientationData;
    bno.getEvent(&orientationData, Adafruit_BNO055::VECTOR_EULER);
    float heading = normalizeAngle(orientationData.orientation.x);

    float error = normalizeAngle(heading - target_direction);
    int steer_val = (int)(error * kp);
    steer_val = constrain(steer_val, -30, 30);
    steer(steer_val);

    if (direction == 1) {
      updateTFLuna(Serial1, distance_right);
      if (distance_right >= 80) {
        target_direction += 90;
        target_direction = normalizeAngle(target_direction);

        while (true) {
          updateTFLuna(Serial1, distance_right);
          bno.getEvent(&orientationData, Adafruit_BNO055::VECTOR_EULER);
          heading = normalizeAngle(orientationData.orientation.x);
          error = normalizeAngle(heading - target_direction);
          steer_val = (int)(error * kp);
          steer_val = constrain(steer_val, -30, 30);
          steer(steer_val);
          digitalWrite(IN1, HIGH);
          digitalWrite(IN2, LOW);
          analogWrite(ENA,  100);
          if (abs(error) <= 10) break;
        }

        counter++;
        steer(0);
        digitalWrite(IN1, HIGH);
        digitalWrite(IN2, LOW);
        analogWrite(ENA, SPEED);
        delay(200);

        while (true) {
          updateTFLuna(Serial1, distance_right);
          if (distance_right < 50 && distance_right > 0) break;
          delay(10);
        }
      }
    }

    else if (direction == 2) {
      updateTFLuna(Serial2, distance_left);
      if (distance_left >= 80) {
        target_direction -= 90;
        target_direction = normalizeAngle(target_direction);

        while (true) {
          updateTFLuna(Serial2, distance_left);
          bno.getEvent(&orientationData, Adafruit_BNO055::VECTOR_EULER);
          heading = normalizeAngle(orientationData.orientation.x);
          error = normalizeAngle(heading - target_direction);
          steer_val = (int)(error * kp);
          steer_val = constrain(steer_val, -30, 30);
          steer(steer_val);
          digitalWrite(IN1, HIGH);
          digitalWrite(IN2, LOW);
          analogWrite(ENA,  100);
          if (abs(error) <= 10) break;
        }

        counter++;
        steer(0);
        digitalWrite(IN1, HIGH);
        digitalWrite(IN2, LOW);
        analogWrite(ENA, SPEED);
        delay(200);

        while (true) {
          updateTFLuna(Serial2, distance_left);
          if (distance_left < 50 && distance_left > 0) break;
          delay(10);
        }
      }
    }
  }

  else {
    digitalWrite(IN1, HIGH);
    digitalWrite(IN2, LOW);
    analogWrite(ENA, SPEED);
    delay(1000);
    digitalWrite(IN1, HIGH);
    digitalWrite(IN2, HIGH);
    analogWrite(ENA, 0);
    while (1);
  }
}

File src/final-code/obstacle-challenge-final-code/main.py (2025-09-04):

## Precedence Order - Main Loop
"""
1. Detect Block - imshow if debug
2. Reverse (If block detected)
3. Block Matrix
4. Turn
5. PID (If no blocks at all, speed *= 1.5)
"""

"""
Comment Key
# = Comment
## = Note / ToDo
### = Failsafe
"""

# Importing Modules
import os
import cv2
import numpy as np
import serial
import time
import threading
from gpiozero import LED
from time import sleep

cv2.setNumThreads(2)

SPEED_K = 1
SPEED_K_PARKING = 1
PARKING_SPEED = 60
TURNING_SPEED = 80
SPEED = 100
PARKING_SPEED = int(PARKING_SPEED*SPEED_K_PARKING)
TURNING_SPEED = int(TURNING_SPEED*SPEED_K)
SPEED = int(SPEED*SPEED_K)
SPEED_NO_AURA_FARM = 90

# Debugging
DEBUG = False

# Serial Values
PORT = "/dev/ttyUSB0"
BAUDRATE = 115200

LIDAR_PORT = None

# Movement
DIRECTION = None
KP = 1.0
COUNTER = 0
COUNTER_MAX = 5
target_angle = 0
BLOCK_MULITPLIER_GREEN_ANTI = 1.5

# Logic
BACK_AFTER_TURN_TIME = 0.8
BACK_BEFORE_TURN_TIME = 1.5
last_turn = time.time()
last_cooldown = time.time()
last_block_pass = time.time()
COOLDOWN = 3
InnerStuckFailsafeFlag = False
OuterStuckFailsafeFlag = False

# Data
data = None
angle, left, front, right, ir = None, None, None, None, None

# Camera Settings
BRIGHTNESS = 0
CONTRAST = 3.0
GAMMA = 0.7
inv_gamma = 1.0 / GAMMA
table = np.array([(i / 255.0) ** inv_gamma * 255 for i in np.arange(256)]).astype("uint8")

# Image Processing Values
red_lower   = np.array([0, 167, 120])
red_upper   = np.array([255, 255, 255])
green_lower = np.array([0, 0, 0])
green_upper = np.array([255, 87, 255])
blue_lower  = np.array([0, 137, 0])
blue_upper  = np.array([255, 177, 92])
magenta_lower = np.array([0, 160, 0])
magenta_upper = np.array([255, 255, 130])

led = LED(3)
led.off()

colors = {
    "red": (0, 0, 255),
    "green": (0, 255, 0),
    "blue": (255, 0, 0),
    "orange": (255, 165, 0)
}

masks = {
    "red": (red_lower, red_upper),
    "green": (green_lower, green_upper),
    "blue": (blue_lower, blue_upper)
}

COLOR_RANGES = {
    "red":    ([0, 184, 108], [255, 255, 255]),
    "green":  ([0, 0, 0],     [255, 101, 255]),
    "blue":   ([0, 153, 0],   [255, 186, 90]),
    "orange": ([0, 130, 150], [255, 255, 255])
}

MIN_AREA = {
    "red": 500,
    "green": 500,
    "blue": 300
}

class ThreadedVideoCapture:
    """
    Drop-in replacement for cv2.VideoCapture that:
    - sets V4L2 MJPG (lighter on Pi CPU)
    - shrinks internal buffer to 1 (no multi-frame lag)
    - runs a grab thread keeping only the most recent frame
    - exposes read()/isOpened()/release() just like OpenCV
    """
    def __init__(self, device="/dev/video1"):
        # Allow overriding via env without touching logic
        w = int(os.getenv("CAM_W", "1280"))
        h = int(os.getenv("CAM_H", "720"))
        fps = int(os.getenv("CAM_FPS", "30"))

        self.cap = cv2.VideoCapture(device, cv2.CAP_V4L2)
        if not self.cap.isOpened():
            print("Error: Cannot open camera")
            raise SystemExit(1)

        # Use MJPG; many USB webcams support it and it slashes CPU usage on Pi
        self.cap.set(cv2.CAP_PROP_FOURCC, cv2.VideoWriter_fourcc(*"MJPG"))
        self.cap.set(cv2.CAP_PROP_FRAME_WIDTH, w)
        self.cap.set(cv2.CAP_PROP_FRAME_HEIGHT, h)
        self.cap.set(cv2.CAP_PROP_FPS, fps)
        # Keep buffer tiny to avoid latency
        try:
            self.cap.set(cv2.CAP_PROP_BUFFERSIZE, 1)
        except Exception:
            pass

        # Optional exposure/brightness tweaks (preserve your BRIGHTNESS via postprocess)
        # self.cap.set(cv2.CAP_PROP_BRIGHTNESS, 0.5)

        self.lock = threading.Lock()
        self.frame = None
        self.running = True
        self.t = threading.Thread(target=self._loop, daemon=True)
        self.t.start()

        # Warmup: wait until we have a frame
        t0 = time.time()
        while self.frame is None and (time.time() - t0) < 2.0:
            time.sleep(0.01)

    def _loop(self):
        while self.running:
            ok, f = self.cap.read()
            if not ok:
                continue
            with self.lock:
                self.frame = f

    def read(self):
        # returns (ret, frame) like cv2.VideoCapture
        with self.lock:
            if self.frame is None:
                return False, None
            return True, self.frame.copy()

    def isOpened(self):
        return self.cap.isOpened()

    def release(self):
        self.running = False
        try:
            self.t.join(timeout=0.5)
        except Exception:
            pass
        self.cap.release()

cap = ThreadedVideoCapture("/dev/video0")

# Logic Constants
program_start_time = time.time()
red_turning_values = [0, 0, 0, 0, 0, 0, 0, 5, 10, 15, 0, 10, 15, 25, 30, 5, 10, 15, 25, 35, 0, 0, -1, -1, -1]
red_turning_values_4th_turn_anti = [-5, 0, 0, 0, 0, -5, 0, 5, 10, 15, -5, 10, 15, 25, 30, -5, 10, 15, 25, 35, -5, 0, -1, -1, -1]
red_turning_values_less_than_3000 = [0, 0, 0, 0, 0, 0, 0, 5, 20, 25, -10, 10, 15, 25, 30, -10, 10, 15, 25, 35, 0, 0, -1, -1, -1]
green_turning_values = [0, 0, 0, 0, 0, -15, -10, -5, 0, 0, -30, -25, -15, -10, 0, -35, -25, -15, -10, -5, -1, -1, -1, 0, 0]
green_turning_values_4th_turn_clock = [0, 0, 0, 0, 5, -15, -10, -5, 0, 5, -30, -25, -15, -10, 5, -35, -25, -15, -10, -5, -1, -1, -1, 0, 0] ## TODO: NEED TO BE UPDATED
green_turning_values_less_than_3000 = [0, 0, 0, 0, 0, -25, -20, -5, 0, 0, -35, -30, -15, -10, 0, -35, -25, -15, -10, -5, -1, -1, -1, 0, 0]

# Setting Up Serial
ser = serial.Serial(PORT, BAUDRATE, timeout=1)
time.sleep(2) # Let ESP32 Initialize

# Functions
# Logic Functions
def normalize_angle(angle):
    if angle > 180:
        angle -= 360
    return angle

def angle_diff(target, current):
    diff = target - current
    while diff <= -180:
        diff += 360
    while diff > 180:
        diff -= 360
    return diff

# Communication Functions
def get_front(port=None, baud=115200, timeout=0.1):
    global DIRECTION
    if DIRECTION == "anticlocwise":
        port = "/dev/ttyAMA3"
    else:
        port = "/dev/ttyAMA0"
    if not port:
        return None
    try:
        with serial.Serial(port, baud, timeout=timeout) as ser:
            # Read 9 bytes (full TF-LUNA frame)
            frame = ser.read(9)
            if len(frame) != 9:
                return None

            # Check header (0x59 0x59)
            if frame[0] != 0x59 or frame[1] != 0x59:
                return None

            # Extract distance (low byte + high byte)
            dist = frame[2] | (frame[3] << 8)
            return dist if dist >= 0 else None
    except serial.SerialException as e:
        print(f"[ERROR] Failed to read from {port}: {e}")
        return None
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

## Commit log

2025-06-27 commit-27.06.2025: docs: add basic details of prototype 1
2025-06-27 commit-27.06-2025#2: docs: updated the documentation of prototype 1
2025-06-28 commit-28.06.2025: feat: add ESP32 programs for BNO055 and MG90 servo motor
2025-06-28 commit-28.06.2025#2: feat: add ESP32 programs for L293D motor driver IC and TF-Luna LiDAR sensor
2025-06-29 commit-29.06.2025: feat: add programs for steering while driving and driving in a straight line
2025-06-29 commit-29.06.2025#2: feat: add program for ESP32 clockwise wall following
2025-07-03 commit-03.07.2025: feat: add programs for RGB and HSV mask calibration for detecting and classifying blocks
2025-07-05 commit-05.07.2025: refactor: add print commands in HSV and RBG calibration programs
2025-07-05 commit-05.07.2025#2: feat: added 3d model for servo mount
    [servo_mount.stl]
2025-07-16 commit-16.07.2025: feat: add program for ESP32 and Raspberry Pi communication
2025-07-17 commit-17.07.2025: feat: add program for centering servo for testing
2025-08-20 commit-20.08.2025: feat: update ESP32 and Raspberry Pi communication
2025-08-20 commit-20.08.2025#2: feat: add programs for camera settings and mask calibration
2025-08-25 commit-25.08.2025: feat: add 3d models for adapters and LiDAR mount
    [motor-axle-adapter.stl, servo-axle-adapter.stl, servo_mount.stl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]
2025-08-25 commit-25.08.2025#3: feat: add chassis assembly guide
2025-08-26 commit-26.08.2025: chore: add models for servo mount
    [servo-mount-bottom.stl, servo-mount-top.stl]
2025-08-28 commit-28.08.2025: docs: add README.md
    [MobilitySystem.fzz, PowerManagement.fzz, SensorManagement.fzz]
2025-09-04 commit-04.09.2025: docs: update README.md
    [PowerManagement.fzz, SensorManagement.fzz]
